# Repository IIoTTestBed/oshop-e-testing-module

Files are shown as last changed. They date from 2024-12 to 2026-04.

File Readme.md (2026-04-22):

# OSHOP Electronics Testing Module (OSH Demonstrator)

This Electronics Testing Module (OSHOP-E-Testing-Module) is an Extension of the IIoT Test Bed of the HTW Dresden. It is intended to be designed as an Open Source Hardware component within the scope of the "Open Source Hardware Innovation Platform" (OSHOP) project. In addition to its function in the IIoT Test Bed, it serves the analysis and evaluation of best practices in development under Open Source Hardware principles. The repository thus serves more for documenting the strengths and weaknesses of the Open Source concept for the development of machinery and equipment at the current time.

[TOC]

## Description

The OSHOP-E-Testing-Module extends the IIoT Test Bed of the Smart-Production-Systems group at the HTW Dresden with an Electronics Test Module. The IIoT Test Bed represents a simplified Industry 4.0 production line and demonstrates the flexible connection of several modules that can adapt to a specific product. The task of the OSHOP-E-Testing-Module is the electronic testing of a device (simplified model). The development of the OSHOP-E-Testing-Module takes place within the framework of the OSHOP project using "Open Source principles". The IIoT Test Bed is based on CP Factory Modules from the company Festo. Similarly, the OSHOP-E-Testing-Module will initially only be usable within this environment. The general value of this demonstrator lies therefore in the gained insights to simplify the development of OSH and to further advance it.

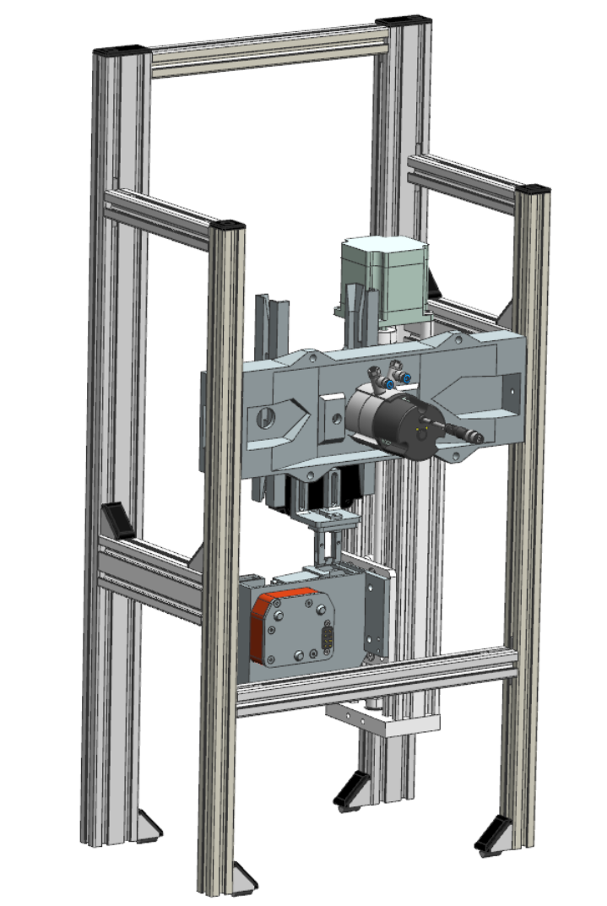
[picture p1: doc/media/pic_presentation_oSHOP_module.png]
Overview of the OSHOP-E-Testing-Module


## Procedure and Goals

- Investigation of various aspects:
    - Applicability of Git for hardware development (Open Source Hardware)
        - Version control
        - Change tracking
        - Dependency management
            - Nesting of components as Git submodules
        - Branching for collaborative work
    - Interaction/mix of proprietary and OSH designs
        - Integration of external components
- Development of an overarching intuitive/ergonomic project structure in line with frequently encountered structures in Open Source Software (OSS) repositories
    - Comparison and evaluation of various standards and OSH repositories
        - `osh-dir-std`
        - `DIN EN 81346` -> Naming conventions
    - Naming conventions
        - Testing practical naming regulations
- Bill of Materials (BOM)
    - Development of a BOM structure
    - Long-term testing of automatic generation of a BOM
        - Evaluation of submodules
        - Development of possibilities for manual modification
- Project documentation
    - Application of established procedures in OSS development
        - Documentation based on Markdown (`Readme.md`) and testing of subsequent toolchains
        - Possibilities of automation testing ("Docs Pipeline")
    - Documentation of use cases as a basis for further development in the OSHOP project
        - General development process
            - Component modeling
            - Research and integration of external free and proprietary designs
        - Git workflow
    - Identification of necessary documents regarding legal aspects
        - Function description
            - `TRL` evaluation (Basis for legal questions)
        - Assembly instructions
        - Technical documentation
            - Schematics (Pneumatics, Electricity)
            - Software
        - Software documentation
        - Hazard assessment
            - FMEA
        - Tests/Simulations
- Licensing
    - Checking compatibility of used licenses
        - Copyleft
    - License management via `REUSE` according to `SPDX`

## Status

At the moment, the demonstrator has not yet reached a functional state. Currently, the programs for controlling the drives and pneumatics are being written. Therefore, an assembly instruction and BOM can currently not be provided, as the current development processes affect the existing constructions and require constant adjustments. Furthermore, many used parts, such as hoses, cables, screws, etc., are not fully modeled. Changes therefore require constant manual updating of the documents.

This public repository includes only freely licensed designs. Proprietary models have been removed.

## Current TODOs

- TODO:
    - [ ] Manage licenses using REUSE
    - [ ] Remodeling of proprietary models to complete the public repository
    - [ ] Assembly instructions
    - [ ] Technical documentation
        - [ ] Schematics
        - [ ] Software
    - [ ] Control software
    - [ ] Documenting Git workflow
        - [ ] Branching model
    - [ ] BOM
    - [ ] Complete implementation of the documented conventions
        - [ ] Uniform naming of all files
        - [ ] Outsourcing of subassembly groups and parts into separate repositories (Submodules)

- DONE:
    - [x] Basic structuring of the project
    - [x] Initialization of Git repository and migration of models

## Dependencies

- Arduino
    - Control of the linear drive (Z-axis)
- Siemens NX
    - Needed for modifying CAD designs
- CP Factory
    - For controlling and powering the module (Electric, Pneumatic)
    - Connection to SPS
    - Festo Tec2Screen/iEasyLab for pneumatic control/tool change mechanism
- Proprietary Models
    - This public repository does not include proprietary CAD models
    - See `doc/functional_hardware_structure.md` to see which components were excluded
- Measure-Tools for the tool changer:
    - Tester:
        - `TinyProbe`: <https://github.com/wagiminator/ATtiny13-TinyProbe>
        - `Continuity Tester`: <https://github.com/wagiminator/ATtiny13-ContinuityTester>

## Project Structure

The project structure is based on the considerations of the `osh-dir-std`, but deviates from it to make it more understandable from the perspective of a constructor. This structure will undergo further changes during development.

- `doc`
    - Documentation
    - `drafts`
        - Notes and considerations, unstructured, documentation of the development process
    - `media`
        - Rendered views
        - Animations
- `src`
    - `electronic` (anticipated)
    - `hardware`
        - Contains all source CAD-files in Siemens NX `.prt` format
        - See `doc/functional_hardware_structure.md` for detailed information about the assembly and submodules
        - `printing`: STL files for printing, prototyping, analogous to the `build` or `bin` directory in software development
            - May be dropped in the future if we are able to automate the generation
    - `software`
- `LICENSES`
    - REUSE/SPDX license files for managing different licenses
- `LICENSE.md`
    - Overview of used licenses in the project
- README.md
    - Project description, general information

## License

For all self-created components, source texts, and documentation resources, the following licenses apply:

- Software: `AGPL`
- Hardware/Electronics: `CERN-OHL-S`
- Documentation: `CC-BY-SA-4.0`

Please refer the [documentation](doc/functional_hardware_structure.md) for detailed information about licensing of the used models.

## Versioning

As a convention for meaningful version numbers, we use the [Semantic Versioning Specification v2.0.0](https://semver.org/).

The version number has the following structure `MAJOR.MINOR.PATCH`.
An increase in each of the places means:

- `MAJOR` version when you make incompatible interface changes
- `MINOR` version when you add new features with backward compatibility
- `PATCH` version when you make backward compatible bug fixes or other minor changes

## Branching

For development with Git, the following branching structure was initially chosen:

| branch | meaning |
| --- | --- |
| `main` | releases of tested and documented versions |
| `documentation` | documentation of successfully tested changes merged from `testing`  |
| `testing` | testing of merged changes from `development` |
| `development` | general development |
| `dev/<feature-name>` | separated development of new feature <feature-name> |

Since proprietary models are not allowed in the public repository, this branching structure currently only exists in the internal repository.
Therefore, an OS variant is published at certain intervals.
The following diagram is intended to illustrate the workflow.

```mermaid
%%{init: {
    'logLevel': 'debug',
    'theme': 'base',
    'gitGraph': {
        'mainBranchOrder': 1
    }
}}%%
gitGraph LR:
    commit
    branch documentation order: 10
    branch testing order: 20
    branch development order: 30
    commit
    commit
    commit
    checkout testing
    merge development
    commit
    commit
    checkout documentation
    merge testing
    commit
    checkout main
    merge documentation tag: "1.0.0"
    branch "doc_osh:github/main" order: 0
    commit
    checkout main
    branch bugfix order: 21
    commit
    checkout testing
    merge bugfix
    commit
    checkout documentation
    merge testing
    checkout main
    merge documentation tag: "1.0.1"
    checkout "doc_osh:github/main"
    merge main
    checkout main
    branch "development'" order: 40
    commit
    branch "dev/feature-0815" order: 41
    commit
    checkout "development'"
    commit
    merge "dev/feature-0815"
    commit
    checkout testing
    merge "development'"
    commit
    checkout documentation
    merge "testing"
    commit
    checkout main
    merge documentation tag: "1.1.0"
    checkout "doc_osh:github/main"
    merge main id: "Clean OSH Repository"
```

**Notes**

- The branches `development` and `development'` are identical and should be displayed in the same line
- `development'` represents a `rebase` on the corresponding commit where development should continue to avoid unnecessary merges
- the plugin used for the diagram `mermaid.js` with `gitGraph` currently does not support `rebase`

## Funding

This OSH demonstrator was created as part of the Open Source Hardware Innovation Platform (OSHOP) project at HTW Dresden and is funded by the Federal Ministry for Research, Technology and Space as part of the T!Raum initiative.

BMFTR Logo
T!Raum Logo
OSHOP Logo

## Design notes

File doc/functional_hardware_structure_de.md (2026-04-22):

# Functional Structure of the Hardware
- Aufschlüsselung der funktionalen Struktur angelehnt an die DIN EN 81346

- **`e_testing_module.prt`**
    - Hauptbaugruppe
    - Rahmen aus Aluminiumprofilen
        - aus HTW-Bestand
        - TODO: kompatible Produkte recherchieren
        - Konstruktion für Festo CP Factory Modul
- **`base_module`**
    - CPFactory Grundmodul
    - Modell nicht im öffentlichen OSH-Repository enthalten
    - Hersteller/Typ: `Festo `
    - Lizenz: proprietär
    - `band_zubehör.prt`
    - `band.prt`
    - `befestigungs_rails.prt`
    - `festo_base_module_x.prt`
    - `festo_base_module.prt`
- **`linear-motion-guide_lmg`**
    - **`c-beam-linear-actuator-250mm`**
        - Linearführung (Z-Achse)
        - Basis Komponente (Design):
            - Ordner: `original`
            - Format: STEP
            - Quelle: https://grabcad.com/library/c-beam-linear-actuator-250mm-1
            - Hersteller: https://openbuildspartstore.com/c-beam-linear-actuator-bundle/
            - Lizenzvermerk: "This design incorporates OpenBuilds, LLC design work(s) shared Open Source under the CC BY-SA 4.0 License."
            - Datum: 13.06.2023
        - Probleme:
            - verwendet anderes Profil (US/Zoll), Nutensteine nicht kompatibel
            - Lizenzvermerk nur auf Webseite/Plattform vorhanden
            - Lizenz kann vom Urheber zu jedem Zeitpunkt angepasst werden
            - kein Lizenzvermerk direkt in der STEP-Datei
            - keine Lizenzdatei im Downloadarchiv vorhanden
            - dadurch keine Zuordnung zur konkreten Datei zu späterem Zeitpunkt mehr möglich
            - weitere Dokumente (Anleitungen, BOM, etc.) nur über Webseite nicht als gebündeltes Archiv versioniert
        - Steppermotor
            - Hersteller/Typ: `Nema 23`
            - wird über Arduino angesteuert
        - Aluminiumprofil
        - Montageplatten
        - Wellenkupplung
        - **`C-Beam Linear Actuator 250mm_stp.prt`**
            - Siemens NX Import von `original/C-Beam Linear Actuator 250mm.stp`
        - **`c-beam_linear_actuator_sledge.prt`**
            - Schlitten
        - **`c-beam-linear-actuator-spindle.prt`**
            - Spindel
        - **`linear_guide.prt`**
            - Baugruppe
    - **`limit-switch`**
        - Endlagensensoren
        - **`sensor_frame.prt`**
            - Halter
            - selbst konstruiert
            - Author: Valentin Petzold
            - Lizenz: CERN-OHL-S
        - `cad6084_stp.prt`
            - Siemens NX Import von `original/cad6084.stp`
            - Modell nicht im öffentlichen OSH-Repository enthalten
            - Sensoren
            - Basis Komponente (Design):
                - Hersteller/Typ: `Pepperl+Fuchs NBB2-8GM30-E2`
                - Zukaufteil
                - Datei: `original/cad6084.stp`
                - Quelle: https://www.pepperl-fuchs.com/germany/de/classid_143.htm?view=productdetails&prodid=90059
                - Lizenz: CADENAS, proprietär
    - **`mounting_adapter`**
        - **`mounting_adapter.prt`**
- **`module_structure`**
    - **`module_structure.prt`**
- **`tool_changer_system`**
    - **`Actuation_Mechanism`**
        - Hubzylinder um Werkzeugwechsel auszulösen 
        - selbst konstruiert
        - Author: Valentin Petzold
        - Lizenz: CERN-OHL-S
        - `festo_piston_rotating_mount_25mm_hub`
            - Zukaufteil
            - Modell nicht im öffentlichen OSH-Repository enthalten
            - Hersteller/Typ: `Festo ADN-16-20-A-P-A`
            - Basis Komponente (Design):
                - Ordner: `UG3DNX1926`
                - Lizenz:
                    - proprietär
                    - `readme-and-terms-of-use-3d-cad-models.txt`
                        - https://www.cadenas.de/nutzungsbedingungen-3d-cad-modelle
                            - §6 Nutzungsrechte:
                                - "[..] Er darf die abgerufenen Daten ausschließlich zum eigenen Gebrauch nutzen. Das Anfertigen von Kopien oder die Weitergabe an Dritte ist unzulässig."
        - `separator_adapter.prt`
        - `slotted pan head _ se_bolt_female.prt`
        - `slotted pan head _ se_bolt_male.prt`
    - **`Housing`**
        - Gehäuse und Halterung des Werkzeugwechselsystems
        - selbst konstruiert
        - Author: Valentin Petzold
        - Lizenz: CERN-OHL-S
        - `inner_housing_separator.prt`
            - Verbindungselement/Brücke zwischen Basishalter und Werkzeughalter
        - `Mag_Tool_Changer_Baseplate.prt`
            - Basishalter und Verbindung zur Linearführung, hält Werkzeughalter und Verriegelungsmechanismus
        - `shaft_toolhead.prt`
            - Welle, auf der Magnetverriegelung angebracht ist
    - **`Tool_Changer_Head`**
        - `Bearing 619-5.prt`
            - Kugellager, Verbindung des Drehmechanismus der Magneten mit Welle
            - Standardteil, Modell von Grabcad
            - Link: https://grabcad.com/library/bearing-619-5-1
            - Format: STEP
            - Lizenz: keine Angabe, ungeklärt, Nutzungsbedingungen von Grabcad
        - `conical_magnet.prt`
            - konischer Magnet zur Zentrierung des Werkzeugs auf dem Halter
            - Zukaufteil
            - nachkonstruiert nach Produktdatenblatt
            - Author: Valentin Petzold
            - Lizenz: CERN-OHL_S
        - `MagToolChanger_HeadBase.prt`
            - Trägerstruktur/Gehäuse, Verknüpfung zum `Housing` und Wechselmechanismus
            - angepasste Konstruktion siehe `Tool_changer_osh_original_files`
        - `MagToolChanger_Lockplate.prt`
            - drehbare Platte mit Magneten, wird durch Pneumatik-Kolben angetrieben
            - vorher `MagToolChanger_Lockplate_part1.prt`
        - `MagToolChanger_Lockplate_part2.prt`
            - obsolet, da per Druckparameter Hohlraum überbrückt werden kann, Druck also mit einem Modell möglich ist
        - `plate_magtoolchanger_headbase.prt`
            - Abdeckung und Halterung für konische Magneten
        - `tool_changer_rotation_plate.prt`
            - obsolet, erster Entwurf des `tool_storage_system`
    - `Tool_changer_osh_original_files`
        - Werkzeugwechselsystem, OSH
        - Quelle: https://github.com/totaldesaster/toolchanger
        - Lizenz: GPLv3
    - **`Toolhead Assembly_stp.prt`**
- **`tool_storage_system`**
    - Werkzeuglager
    - **`drvs12-rot_motor`**
        - Antrieb zum Schwenken des Werkzeughalters
        - Modell nicht im öffentlichen OSH-Repository enthalten
        - Zukaufteil
        - Hersteller/Typ: `Festo DRVS-12-180-P`
        - Ordner: `UG3DNX1926`
        - Lizenz: Nutzungsbedingungen von CADENAS, <https://www.cadenas.de/nutzungsbedingungen-3d-cad-modelle>, proprietär
        - erweitert mit Endlagensensor: `Festo SRBS-Q12-12`
            - Modelle siehe oben
    - **`mounting`**
        - Aufnahme des Werkzeughalters
        - selbst konstruiert
        - Author: Valentin Petzold
        - Lizenz: CERN-OHL-S
        - **`mounting_storage.prt`**
            - Befestigung des Werkzeuglagers am Rahmen
            - wg. Druckbarkeit in 2 Teile aufgeteilt (`*_{p1|p2}.prt`)
        - **`spacer_storagemount_rotdev.prt`**
            - Abstandshalter zwischen Antrieb und Halterung
            - Justierung des Abstands zwischen Werkzeuglager und Halterung
    - **`tool_holder`**
        - Werkzeughalter
        - selbst konstruiert
        - Author: Valentin Petzold
        - Lizenz: CERN-OHL-S
        - **`tool_storage_part1.prt`**
            - symmetrisch, muss doppelt gedruckt und montiert werden
        - **`spacer_storage_mounting`**
            - Adapter für Flansch zu Werkzeughalter
    - **`tool_locking_system`**
        - Werkzeug Verriegelung
        - **`clamp`**
            - Klemme zur Arretierung des Werkzeugs 
            - `tool_storage_lock_plate`
                - selbst konstruiert
                - Author: Valentin Petzold
                - Lizenz: CERN-OHL-S
                - TODO: Muttern modellieren --> Montageanleitung
        - `dummies`
            - `dummy_piston.prt`
                - Dummy zum testen der mechanischen Verriegeln des Werkzeughalters
                - später durch pneumatischer Kolben ersetzt
            - `pull_clip.prt`
                - Clip zum mechanischen Verriegeln
        - **`piston_actuator/advc-10-10-apa-kurzhub`**
            - Kolben um Klemmung auszulösen
            - Zukaufteil
            - Modell nicht im öffentlichen OSH-Repository enthalten
            - Hersteller/Typ: `Festo ADVC-10-10-APA`
            - Lizenz: CADENAS, proprietär
            - Probleme:
                - verwendete Modelle von Festo waren kleiner als die realen Abmaße des gelieferten Kolbens
        - **`piston_mounting_structure`**
            - Halterung für den Kolben
            - Komponenten:
                - `piston_mounting_frame`
                - `piston_mounting_plate`
            - Probleme:
                - Halter liegt sehr eng an Kolben an, erfordert u.U. immer Anpassung an Modelle anderer Hersteller
                - Befestigungsschrauben nicht mit modelliert
                - könnte eleganter konstruiert werden durch montage am vorderen Ende, eher Konstruktionsschwäche des Kolbens
            - selbst konstruiert
            - Author: Valentin Petzold
            - Lizenz: CERN-OHL-S
        - **`tool_storage_print_vers.prt`**
- **`tools`**
    - `plate_tool_board.prt`
    - `spacer_10x3.6_id3.prt`

- noch nicht im Modell enthalten:
- Treibermodul
    - wandelt Befehle vom Mikrocontroller in elektrische Signale an den Motor um (Rechtecksignal)
    - Hersteller/Typ: `ACT Motor DM 542`
- Microcontroller
    - Hersteller/Typ: `Arduino M0 Pro`
- Pneumatik
    - Ventilinsel
        - Hersteller/Typ: `Festo`
        - TODO: genaue Bezeichnung ergänzen!
- Dockingmodul:
    - Schnittstelle zu Tablet/CP-Factory-Modul
    - Hersteller/Typ: `Festo +G1:XD12`

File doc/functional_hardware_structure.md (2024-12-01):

# Functional Structure of the Hardware
- Breakdown of the functional structure based on DIN EN 81346

- **`e_testing_module.prt`**
    - Main assembly
    - Frame made of aluminum profiles
        - from HTW stock
        - TODO: search for compatible products
        - Construction for Festo CP Factory Module
- **`base_module`**
    - CPFactory base module
    - Model not included in the public OSH-Repository
    - Manufacturer/Type: `Festo`
    - License: proprietary
    - `band_zubehör.prt`
    - `band.prt`
    - `befestigungs_rails.prt`
    - `festo_base_module_x.prt`
    - `festo_base_module.prt`
- **`linear-motion-bearing`**
    - **`c-beam-linear-actuator-250mm`**
        - Linear actuator (Z-axis)
        - Basic component (Design):
            - Folder: `original`
            - Format: STEP
            - Source: https://grabcad.com/library/c-beam-linear-actuator-250mm-1
            - Manufacturer: https://openbuildspartstore.com/c-beam-linear-actuator-bundle/
            - License notice: "This design incorporates OpenBuilds, LLC design work(s) shared Open Source under the CC BY-SA 4.0 License."
            - Date: 13.06.2023
        - Issues:
            - Uses a different profile (US/inch), dowels used in the main assembly are not compatible
            - License notice only available on the website/platform
            - License can be adjusted by the author at any time
            - No license notice directly in the STEP file
            - No license file in the download archive available
            - Therefore, no assignment to the specific file possible at a later time
            - Further documents (instructions, BOM, etc.) only available over the website not versioned as a bundled archive
        - Stepper motor
            - Manufacturer/Type: `Nema 23`
            - Controlled via Arduino
        - Aluminum profile
        - Mounting plates
        - Wave coupling
        - **`C-Beam Linear Actuator 250mm_stp.prt`**
            - Siemens NX import of `original/C-Beam Linear Actuator 250mm.stp`
        - **`c-beam_linear_actuator_sledge.prt`**
            - Sledge
        - **`c-beam-linear-actuator-spindle.prt`**
            - Spindle
        - **`linear_guide.prt`**
            - Assembly
    - **`limit-switch`**
        - End switch sensors
        - **`sensor_frame.prt`**
            - Holder
            - Self-constructed
            - Author: Valentin Petzold
            - License: CERN-OHL-S
        - `cad6084_stp.prt`
            - Siemens NX import of `original/cad6084.stp`
            - Model not included in the public OSH-Repository
            - Sensors
            - Basic component (Design):
                - Manufacturer/Type: `Pepperl+Fuchs NBB2-8GM30-E2`
                - Purchase part
                - File: `original/cad6084.stp`
                - Source: https://www.pepperl-fuchs.com/germany/de/classid_143.htm?view=productdetails&prodid=90059
                - License: CADENAS, proprietary
    - **`mounting_adapter`**
        - **`mounting_adapter.prt`**
- **`module_structure`**
    - **`module_structure.prt`**
- **`tool_changer_system`**
    - **`Actuation_Mechanism`**
        - Piston cylinder to trigger tool change
        - Self-constructed
        - Author: Valentin Petzold
        - License: CERN-OHL-S
        - `festo_piston_rotating_mount_25mm_hub`
            - Purchase part
            - Model not included in the public OSH-Repository
            - Manufacturer/Type: `Festo ADN-16-20-A-P-A`
            - Basic component (Design):
                - Folder: `UG3DNX1926`
                - License:
                    - proprietary
                    - `readme-and-terms-of-use-3d-cad-models.txt`
                        - https://www.cadenas.de/nutzungsbedingungen-3d-cad-modelle
                            - §5 Terms of Use:
                                - "[..] The customer may use the retrieved data for personal uses only."
        - `separator_adapter.prt`
        - `slotted pan head _ se_bolt_female.prt`
        - `slotted pan head _ se_bolt_male.prt`
    - **`Housing`**
        - Housing and mounting of the tool change system
        - Self-constructed
        - Author: Valentin Petzold
        - License: CERN-OHL-S
        - `inner_housing_separator.prt`
            - Connection element/bridge between the base holder and tool holder
        - `Mag_Tool_Changer_Baseplate.prt`
            - Base holder and connection to the linear actuator, holds the tool holder and locking mechanism
        - `shaft_toolhead.prt`
            - Shaft, on which the magnetic lock is mounted
    - **`Tool_Changer_Head`**
        - `Bearing 619-5.prt`
            - Bearing, connection of the rotating mechanism of the magnets with the shaft
            - Standard part, model from Grabcad
            - Link: https://grabcad.com/library/bearing-619-5-1
            - Format: STEP
            - License: none provided, unclear, usage terms of Grabcad
        - `conical_magnet.prt`
            - Conical magnet for centering the tool on the holder
            - Purchase part
            - Redesigned according to product data sheet
            - Author: Valentin Petzold
            - License: CERN-OHL_S
        - `MagToolChanger_HeadBase.prt`
            - Carrier structure/housing, connection to the `Housing` and locking mechanism
            - Adapted construction see `Tool_changer_osh_original_files`
        - `MagToolChanger_Lockplate.prt`
            - Rotating plate with magnets, driven by a pneumatic cylinder
            - Previously `MagToolChanger_Lockplate_part1.prt`
        - `MagToolChanger_Lockplate_part2.prt`
            - Obsolete, as the gap can be bridged with a print parameter, making a print possible with a model
        - `plate_magtoolchanger_headbase.prt`
            - Cover and holder for conical magnets
        - `tool_changer_rotation_plate.prt`
            - Obsolete, first draft of the `tool_storage_system`
    - `Tool_changer_osh_original_files`
        - Tool change system, OSH
        - Source: https://github.com/totaldesaster/toolchanger
        - License: GPLv3
    - **`Toolhead Assembly_stp.prt`**
- **`tool_storage_system`**
    - Tool storage
    - **`drvs12-rot_motor`**
        - Drive for swinging the tool holder
        - Model not included in the public OSH repository
        - Purchase part
        - Manufacturer/Type: `Festo DRVS-12-180-P`
        - Folder: `UG3DNX1926`
        - License: Terms of use by CADENAS, <https://www.cadenas.de/nutzungsbedingungen-3d-cad-modelle>, proprietary
        - Extended with end stop sensor: `Festo SRBS-Q12-12`
            - Models see above
    - **`mounting`**
        - Mounting of the tool holder
        - Self-constructed
        - Author: Valentin Petzold
        - License: CERN-OHL-S
        - **`mounting_storage.prt`**
            - Mounting of the tool storage to the frame
            - Due to printability, divided into 2 parts (`*_{p1|p2}.prt`)
        - **`spacer_storagemount_rotdev.prt`**
            - Spacer between drive and mounting
            - Adjustment of the distance between tool storage and mounting
    - **`tool_holder`**
        - Tool holder
        - Self-constructed
        - Author: Valentin Petzold
        - License: CERN-OHL-S
        - **`tool_storage_part1.prt`**
            - Symmetrical, must be printed and mounted twice
        - **`spacer_storage_mounting`**
            - Adapter for flange to tool holder
    - **`tool_locking_system`**
        - Tool locking
        - **`clamp`**
            - Clamp for securing the tool
            - `tool_storage_lock_plate`
                - Self-constructed
                - Author: Valentin Petzold
                - License: CERN-OHL-S
                - TODO: Model screws --> Assembly instructions
        - `dummies`
            - `dummy_piston.prt`
                - Dummy for testing the mechanical locking of the tool holder
                - Later replaced by a pneumatic piston
            - `pull_clip.prt`
                - Clip for mechanical locking
        - **`piston_actuator/advc-10-10-apa-kurzhub`**
            - Piston to trigger clamping
            - Purchased part
            - Model not included in the public OSH repository
            - Manufacturer/Type: `Festo ADVC-10-10-APA`
            - License: CADENAS, proprietary
            - Issues:
                - The Festo models used were smaller than the actual dimensions of the delivered piston
        - **`piston_mounting_structure`**
            - Mounting for the piston
            - Components:
                - `piston_mounting_frame`
                - `piston_mounting_plate`
            - Issues:
                - The mounting is very tight on the piston, requires adjustment for models from other manufacturers
                - Mounting screws not modeled
                - Could be more elegantly constructed by mounting at the front end, rather a construction weakness of the piston
            - Self-constructed
            - Author: Valentin Petzold
            - License: CERN-OHL-S
        - **`tool_storage_print_vers.prt`**
- **`tools`**
    - `plate_tool_board.prt`
    - `spacer_10x3.6_id3.prt`

- not yet included in the model:
- Driver module
    - Converts commands from the microcontroller into electrical signals for the motor (rectangular signal)
    - Manufacturer/Type: `ACT Motor DM 542`
- Microcontroller
    - Manufacturer/Type: `Arduino M0 Pro`
- Pneumatics
    - Valve assembly
        - Manufacturer/Type: `Festo`
        - TODO: Add exact designation!
- Docking module:
    - Interface to tablet/CP-Factory module
    - Manufacturer/Type: `Festo +G1:XD12`

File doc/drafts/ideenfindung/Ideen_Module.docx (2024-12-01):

Ventilinsel:

https://www.thingiverse.com/thing:3186352

https://www.thingiverse.com/thing:3142024

https://www.thingiverse.com/thing:3141922

https://www.thingiverse.com/thing:1581203

https://www.thingiverse.com/thing:3985559

https://www.thingiverse.com/thing:2798873

https://www.thingiverse.com/thing:2326265

https://www.thingiverse.com/thing:3808689

https://www.thingiverse.com/thing:2926583

https://www.thingiverse.com/thing:2873796

https://www.thingiverse.com/thing:4754779

https://www.thingiverse.com/thing:2738707

https://www.thingiverse.com/thing:3066355

Einkaufliste:

Pneumatikzylinder:

https://www.pneumaticshop.de/Pneumatikzylinder/

https://www.smc.eu/de-de/produkte/cqs~16708~nav?productId=164339&partNumber=CDQSB12-25D

https://www.reichelt.de/kompaktzylinder-c9585.html?&nbc=1

https://www.festo.com/de/de/p/kompaktzylinder-doppeltwirkend-id_ADN_S/?page=0

https://pneumatikteam.de/pneumatik/zylinder/kurzhubzylinder/

https://www.ventile24.de/cdqsyb25-5dc-smc-pneumatik-c-d-qsy-druckluftzylinder-gleichmassig-leichtlauf-doppeltwirkend-eingebauter-magnetring-durchgangsbohrung-gewinde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

https://www.nettechnic.de/pneumatischer-kompaktzylinder-doppeltwirkend-20x20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

Pneumatischer Schwenkantrieb:

https://www.smc.eu/de-de/produkte/crb2-z~124774~nav?productId=124776&partNumber=CDRB2FWU20-90DZ

https://de.rs-online.com/web/c/pneumatik-und-hydraulik/pneumatik-zylinder-und-antriebe/pneumatische-drehantriebe/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

https://www.landefeld.de/artikel/de/drvs-6-180-p-1845707-schwenkantrieb/OT-FESTO057650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

Drehverteiler Druckluft:

https://www.festo.com/de/de/p/drehverteiler-id_GF/?page=0&q=~%3AfestoSortOrderScored

oder:

https://www.festo.com/de/de/a/177717/?q=~:festoSortOrderScored

+

https://www.landefeld.de/artikel/de/qsr-m5-6-153527-rotations-steckverschraubung/OT-FESTO015490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

Ventilinsel:

https://www.landefeld.de/artikel/de/vqc4301r-51-smc-53-wegeventil/OT-SMC069682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

Steckverschraubungen:

https://www.festo.com/de/de/p/steckverschraubung-id_QS/?page=0

Magnete:

https://deinemagneten.de/produkt/neodym-magnete-o-10x3-mm-n52-scheiben-rundmagnet-starkmagnete-supermagnete/

https://www.magnet-shop.net/neodym-magnete/scheibenmagnete/scheibenmagnet-10.0-x-1.0-mm-n35-nickel-haelt-500-g

quaderscheibe.

https://www.magnet-shop.net/neodym-magnete/quadermagnete/quadermagnet-10.0-x-10.0-x-2.0-mm-n45-nickel-haelt-1.2-kg

Kegel und Senke-Magnet:

https://www.first4magnets.com/de/magnetmaterialien-standardbaugruppen-c150/10mm-durchmesser-x-2mm-dicke-x-3mm-c-sink-neodym-magnet-1-2kg-zugkraft-p2446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

Tools:

Testmodule:

-Shaker

-Lötstellenprüfer

-Gewichtsprüfer

Produktionsmodule:

-Handlager zu Magazin Befüller

-Sicherung entnehmen

-Handlager Sensorik

-2-Achs Roboter

-Werkzeugwechsleraufnahme (flex führung und stromversorgung)

-modifizierter Carrier

-Kistenhub

-Transportmodul zwischen zwei Lagern

https://www.google.com/url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 (https://www.google.com/url?psig=AOvVaw2psAzcrv_vjG3QuWZ-ws1R&cd=vfe)

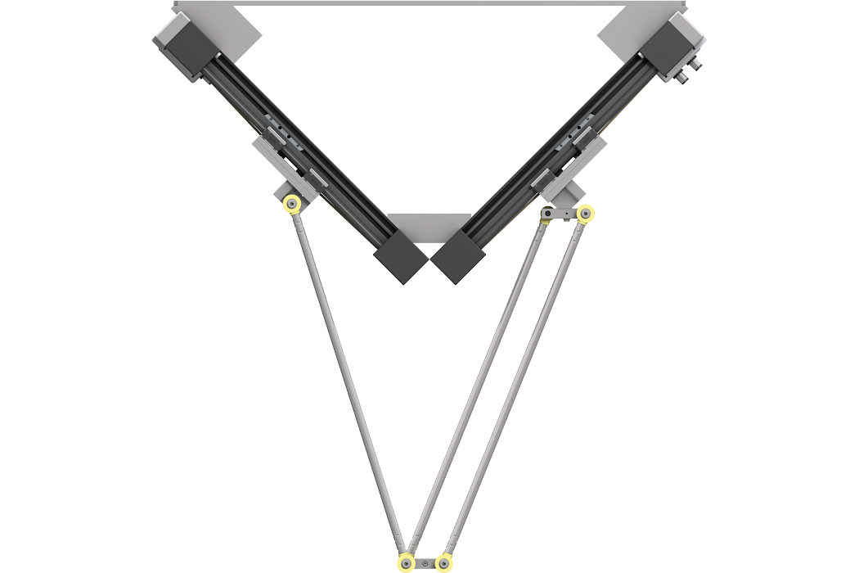
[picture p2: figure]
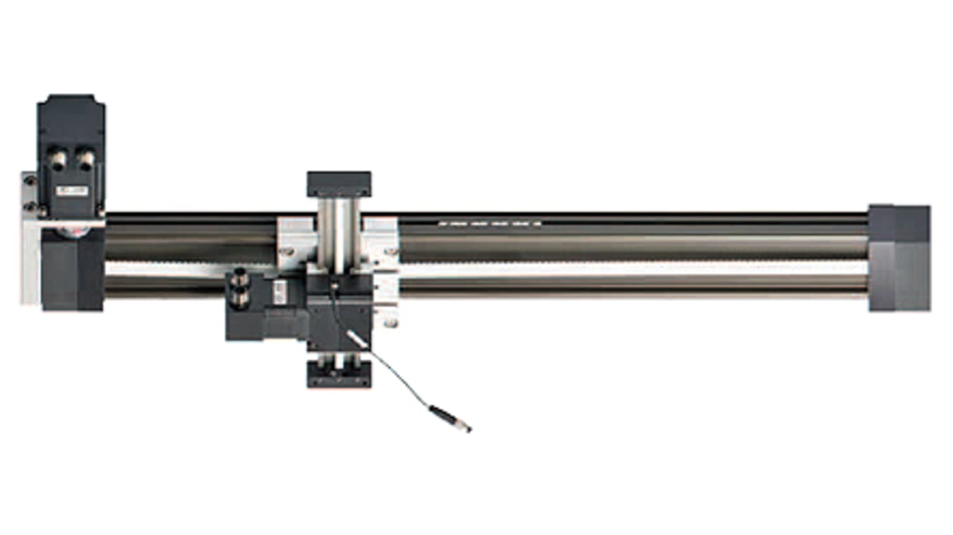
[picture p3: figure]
Igus DLE-LG-0001 2-Achsen Linearer Roboter, Arbeitsraum 500 x 100mm, bis 2.5kg | RS
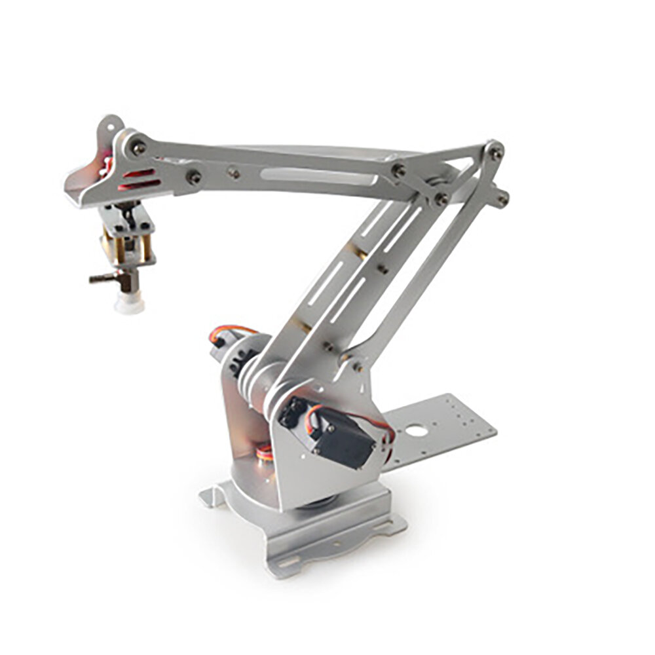
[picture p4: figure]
3 DOF Palettierroboterarm 3-Achsen-Roboter DIY 3D-Drucker mit 180 ° MG996R Servo für die Roboterausbildung Sale - Banggood Deutschland sold out-arrival notice-arrival notice

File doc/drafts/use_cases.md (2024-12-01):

# Use Case Teile-Konstruktion
1. Neues Projekt starten
    - Projektordner anlegen (Grundstruktur)

2. Zielbeschreibung
    - grobes Konzept erarbeiten
    - Erfahrung mit oSHOP Projekt:
        - grobe Vorgabe: Entwicklung eines "faszinierenden" Moduls (mit Bewegung etc.) für Festo CP Factory
        - eigenes Ziel: Projekt mit Nutzen für Arbeitsgruppe, daher: Gespräche mit Kollegen was im Moment noch in CP Factory ergänzt werden könnte bzw. bei welchen Konzepten Probleme bestehen
        - Ergebnis: Ideen zu Toolchanger, eigene Idee zur Prüfung der Leiterplatten welche in CP Factory verarbeitet werden (da diese Funktion noch nicht in Fertigungskette vorhanden) --> Kombination dieser Ideen als Ziel des Projekts
    --> Ableiten erster Anforderungen und Rahmenbedingungen (zum Beispiel Breite/Abstand/Art der Schienen zur Montage auf dem CP Factory Modul)

3. Freie Recherche vorhandener Lösungen
    - keine zentrale, herstellerübergreifende Teiledatenbank
        - gute Beispiele: 
            - speziell für Satellitenentwicklung: https://satsearch.co
        - grobe Kategorisierung
            - Material
    - Doppelentwicklung vermeiden
    - einsparen von Entwicklungsaufwand
    - Wenn es keine fertige Lösung gibt, Neuentwicklung:
        - Recherche nach ähnlichen Lösungsansätzen, Konzepten, Prinzipien
            - hauptsächlich Internet, Webseiten
            - rein visuell anhand von Bildern
                - finden von geeigneten CAD-Modellen schwierig, da aktuelle Plattformen sehr viele unprofessionelle (DIY) Lösungen enthalten
            - viele Repositories (z.B. GitHub) nur textuell beschrieben, sehr aufwendig jeden Fund manuell zu prüfen
    - Erfahrung mit oSHOP Projekt:
        - Recherche nach bestehenden Konzepten rund um Thema Tool Changer und Prüf- bzw. Messverfahren von Leiterplatten
        - ``TinyProbe`` and ``TinyTester`` als Konzepte für Messverfahren identifiziert --> wenig Adaption nötig
        - MagToolChanger als Konzept für Werkzeugwechsel identifiziert --> viel Adaption nötig, Anmerkung: bereits der gefundene Ansatz wurde vom Hersteller E3D inspiriert
            - E3D fertigt kommerziell Werkzeugwechselsystem für 3D Drucker unterstützt aber OSH und stellt teilweise Schemata online
    -- >Ergänzen der Grundanforderungen aus 2. um die Anforderungen resultierend aus selektierten Konzepten

    3.1 Nach Taxonomie Maschinenelemente/Standardteile
        - Grund: Adaption oder Ergänzung der selektierten Konzepte aus 2.
        - Beispiel: Pneumatikzylinder
            - bestimmen von Parametern:
                - erforderlicher Hubweg
                - welche Kräfte treten auf
                - Bewegungscharakteristik (linear, kreisbahn, ...)
            - anhand der Parameter Bestimmung des Kolbendurchmessers nach Herstellern (Kataloge, Webseiten)
            - Bewertung Herstellerauswahl hinsichtlich
                - Bauteilgröße
                - Schnittstellen
                    - zu bereits verwendeten Komponenten, wie Pneumatikschläuche
                    - Notwendigkeit von Adaptern
                    - Befestigung
                - Verfügbarkeit von CAD-Modellen:
                    - Festo: sehr gut
        --> Erweiterung der Anforderungen um zusätzliche Bedingungen durch ausgewählte Maschinenelement bzw. Standardteile

    3.2 Patentrecherche bzw. Verletzung Rechte Dritte
        - Wie hoch ist der tendenzielle Schaden im Falle einer Patentrechtsverletzung?
            - Unterlassung der Produktion/Verkauf
            - nachträglicher Erwerb einer Patentlizenz
            - Schadensforderung (Gewinnausfall des Patentinhabers usw.)
        --> Erbringungen ``freedom to operate`` für den Projektentwurf

AB HIER EIN ITERATIONSPROZESS

4. Adaption der gefundenen Lösungsansätze
    - auf die aufgestellten Anforderungen
    - mit den geplanten Maschinenelementen/Standardteilen

5. Entwurf eigener Interfaces anhand zur Verknüpfung der gefundenen (und adaptierten) Lösungsansätze
    - Verknüpfung aller Konzepte zu vollständiger (Unterbaugruppe)-Baugruppe
    --> zum Beispiel durch Entwurf von Gehäusen, Adaptern, Interfaces etc.

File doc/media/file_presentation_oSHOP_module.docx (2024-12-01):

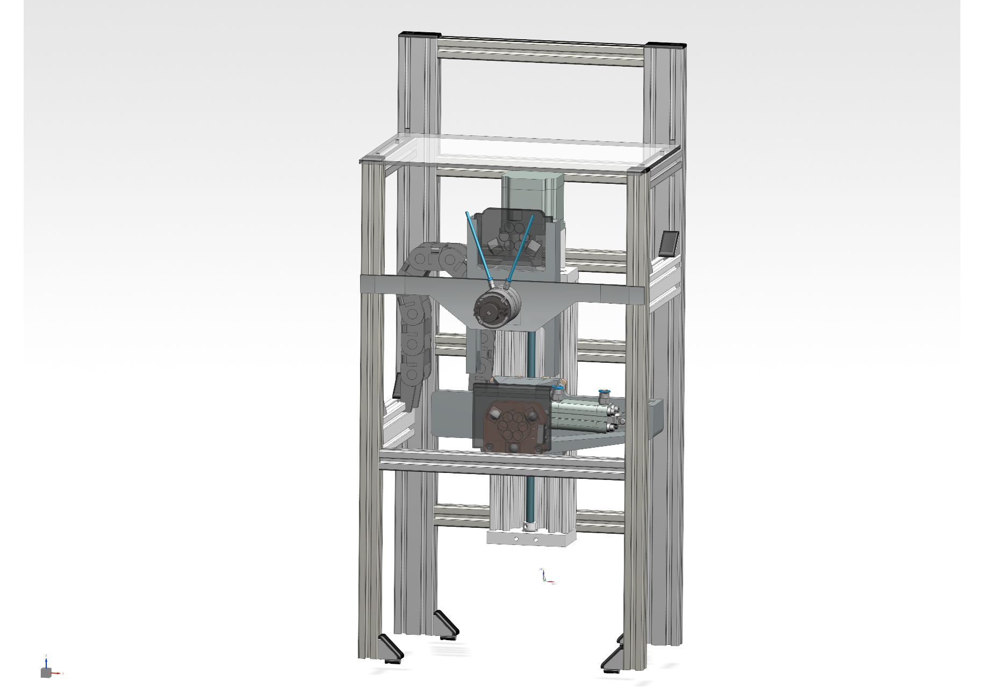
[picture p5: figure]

Open Source Hardware Werkzeuge Zum Beispiel Bestückung mit einer Platine zum Test der elektrischen Funktionalität von Werkstücken

Open Source Energiekette

Publiziert von privatem Entwickler auf Thingiverse.com

CC BY 4.0 License

Open Source Linearführung Vertrieb und Design durch OpenBuilds Store

CC BY-SA 4.0 License

Open Source Werkzeugwechselsystem

Weiterentwickelt für pneumatische Ansteuerung auf einer Linearachse

GNU General Public License V3

Werkzeuglager für Werkzeugwechselsystem

Eigenentwicklung in Vorbereitung zur Publikation als Open Source Hardware

This design incorporates OpenBuilds, LLC (https://openbuilds.com/)design work(s) shared Open Source under the CC BY-SA 4.0 (https://creativecommons.org/licenses/by-sa/4.0/) License.

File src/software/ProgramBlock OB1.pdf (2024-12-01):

## Totally Integrated Automation Portal

# Oshop-Demo_v2 / PLC_1 [CPU 1512SP-1 PN] / Programmbausteine

# Main [OB1]

## Main Eigenschaften Allgemein

Name | Main | Nummer | 1 | Typ | OB | Sprache | KOP
Nummerierung | Automatisch

## Information

Titel | "Main Program Sweep (Cy‐ cle)" | Autor | Kommentar | Familie
Version | 0.1 | Anwenderdefi‐ nierte ID

## Main

Name | Datentyp | Defaultwert | Kommentar

## Input

Initial_Call | Bool | | Initial call of this OB
Remanence | Bool | | =True, if remanent data are available

## Temp

Pos | DInt
RetVal | DInt
tmpByte | Byte

## Constant

# Netzwerk 1:

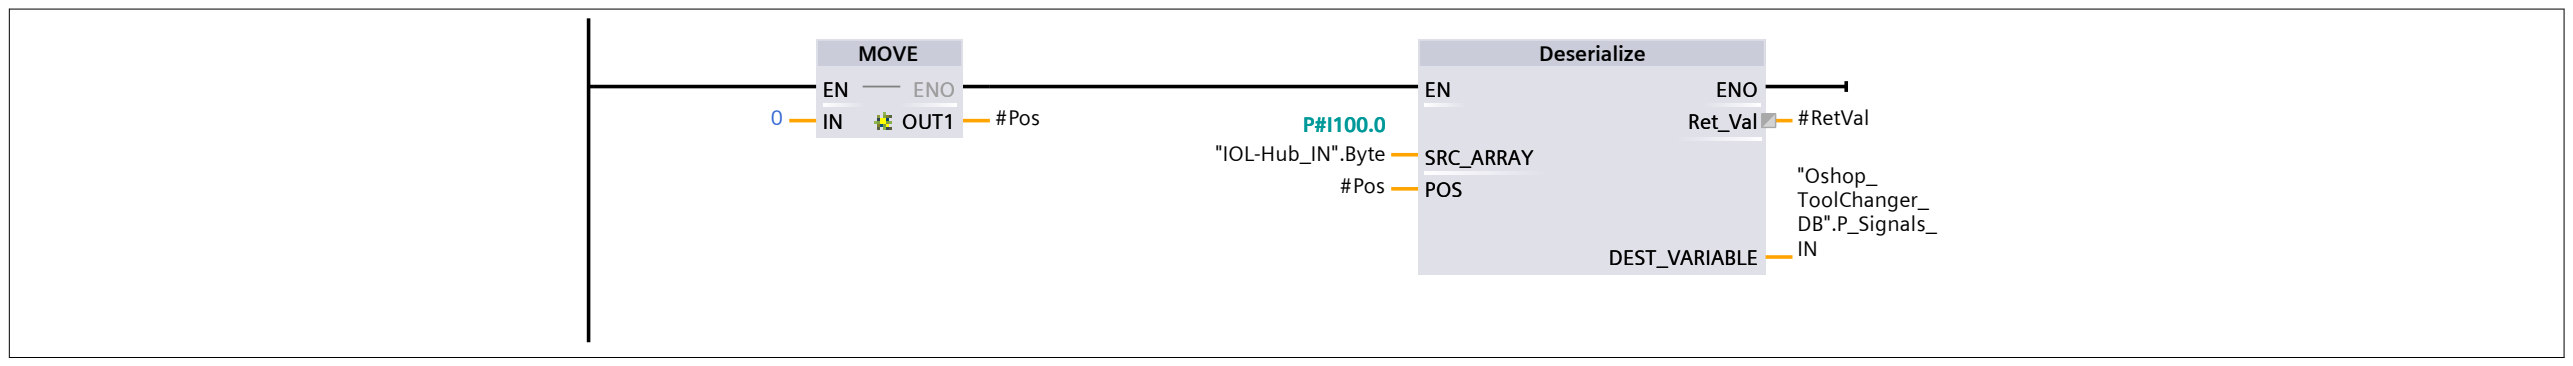
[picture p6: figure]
MOVE; Deserialize; 0 #Pos; "IOL-Hub_IN".Byte P#I100.0; #Pos; #RetVal; "Oshop_ ToolChanger_ DB".P_Signals_ IN; ENO OUT1; SRC_ARRAY POS; ENO Ret_Val; DEST_VARIABLE

# Netzwerk 2:

"Tool_Select"

%FB2

"Tool_Select_DB"

%DB3

"Taster_WH_1"

%I0.1

"Taster_WH_2"

%I0.2

"Lampe_WH_1"

%Q0.1

"Lampe_WH_2"

%Q0.2

0

EN

Button_1

Button_2

ENO

Lamp_1

Lamp_2

ToolNumber EN

Button_1

Button_2

ENO

Lamp_1

Lamp_2
ToolNumber

# Netzwerk 3:

"Oshop_ToolChanger"

%FB1

"Oshop_
ToolChanger_
DB"

%DB1

"Taster_Grün"

%I0.0

"Tool_Select_ DB".ToolNumber

... EN

Start

UseTool
P_Signals_IN

ENO

P_Signals_OUT EN

Start

UseTool
P_Signals_IN

ENO
P_Signals_OUT

# Netzwerk 4:

FILL_BLK

0
1 "IOL-Hub_OUT".
Byte[1]

%QB101

EN
IN
COUNT

ENO

OUT

# Netzwerk 5:

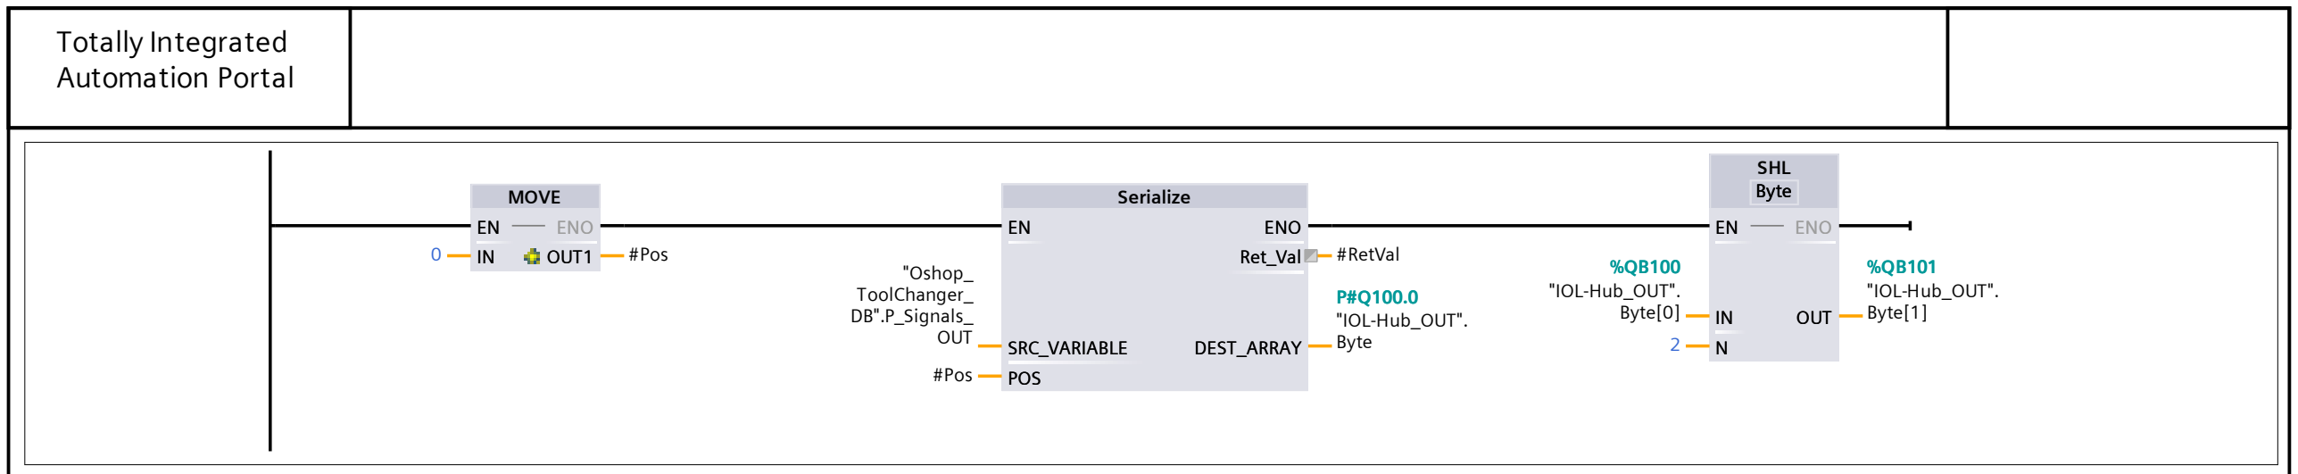
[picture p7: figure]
Totally Integrated Automation Portal; MOVE; Serialize; SHL Byte; 0 #Pos; "IOL-Hub_OUT". Byte; "IOL-Hub_OUT". Byte[0]; "IOL-Hub_OUT". Byte[1]; ENO OUT1; SRC_VARIABLE POS; ENO Ret_Val; DEST_ARRAY; ENO; OUT; Byte EN; Byte

"Oshop_ ToolChanger_ DB".P_Signals_ OUT #Pos | #RetVal

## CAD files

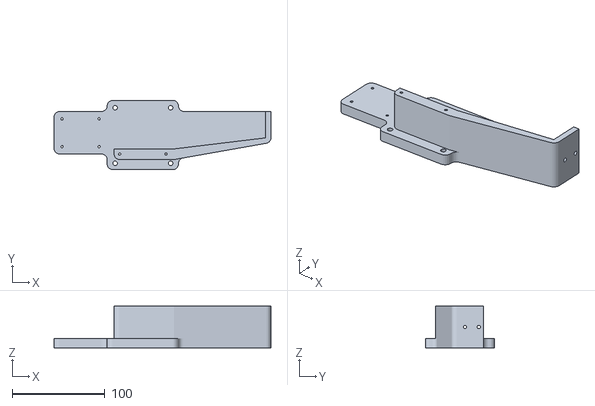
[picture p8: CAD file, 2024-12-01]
gen/manuf/fdm/Mag_Tool_Changer_Baseplate.stl
234.5 x 74.8 x 45.0

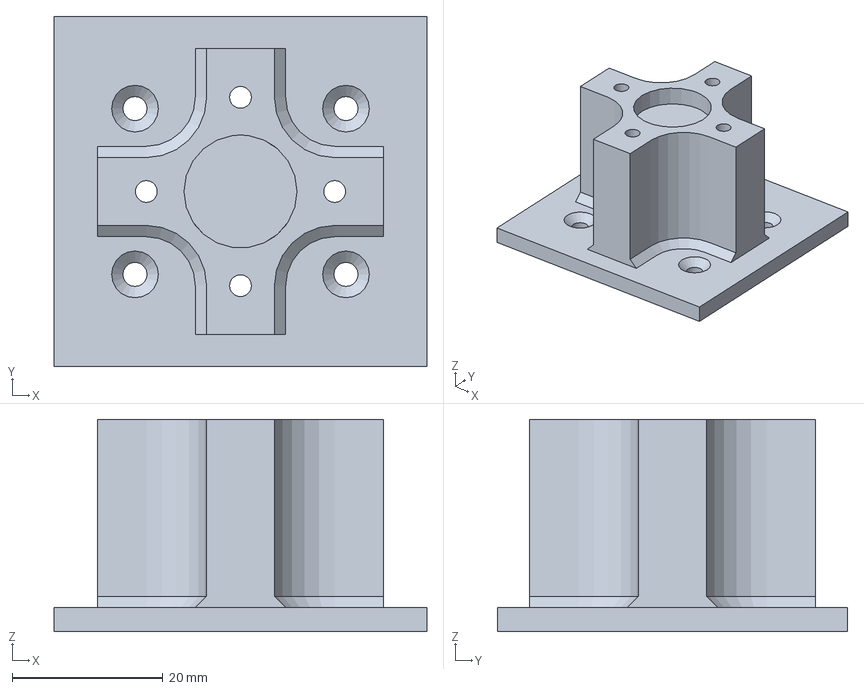
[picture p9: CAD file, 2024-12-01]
gen/manuf/fdm/new/drag_chain.3mf
49.5 x 46.5 x 28.2 mm

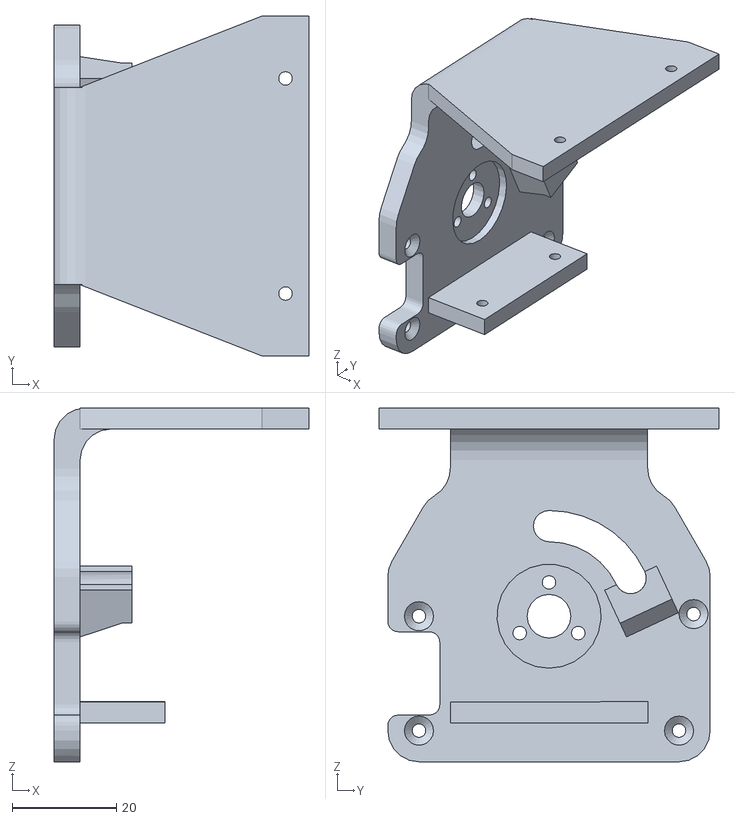
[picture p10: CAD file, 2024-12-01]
gen/manuf/fdm/new/lennart/inner_housing_separator_2.stl
49.0 x 65.4 x 68.0

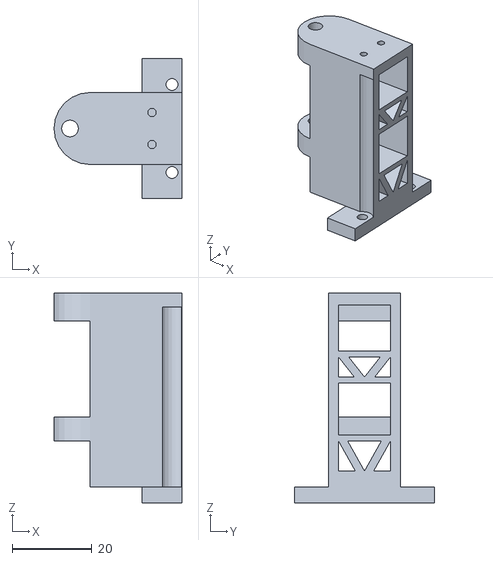
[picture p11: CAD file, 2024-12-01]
gen/manuf/fdm/new_2024/piston_mounting_frame_a_guiding_1.stl
32.0 x 35.0 x 52.5

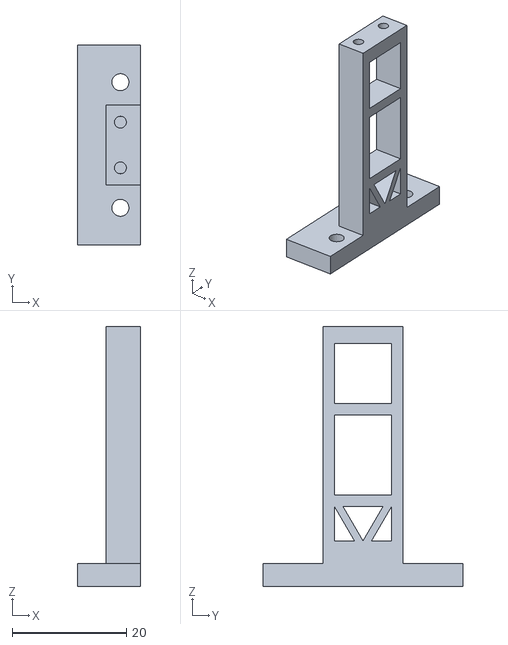
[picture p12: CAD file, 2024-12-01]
gen/manuf/fdm/new/storage_piston_mount.stl
11.0 x 35.0 x 45.5

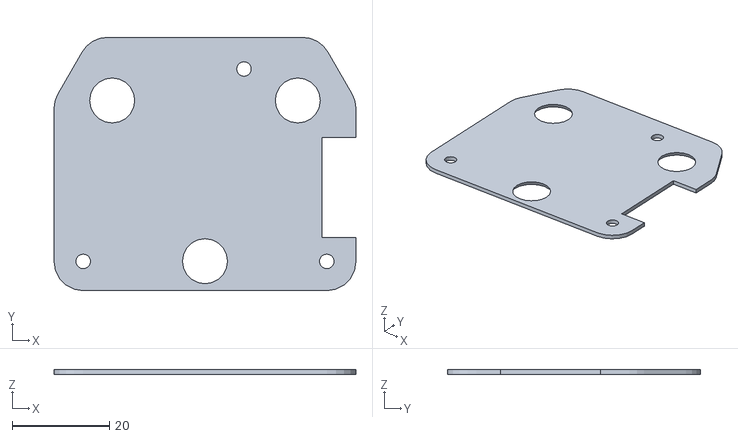
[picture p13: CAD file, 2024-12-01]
gen/manuf/fdm/plate_magtoolchanger_headbase.stl
62.0 x 52.0 x 1.00

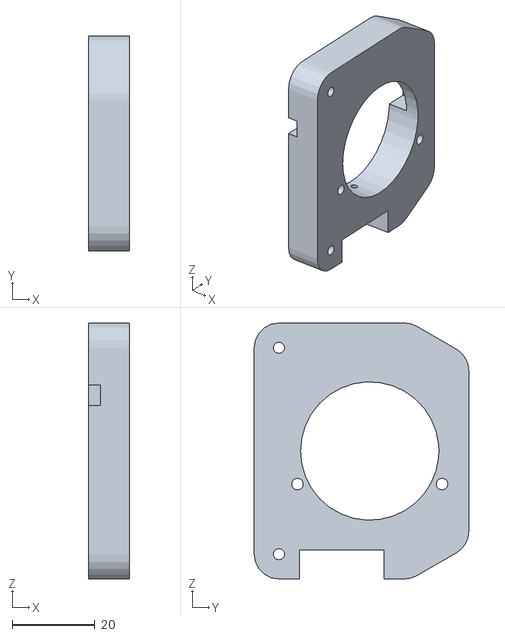
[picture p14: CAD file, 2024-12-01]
gen/manuf/fdm/MagToolChanger_HeadBase_1.stl
10.0 x 52.0 x 62.0

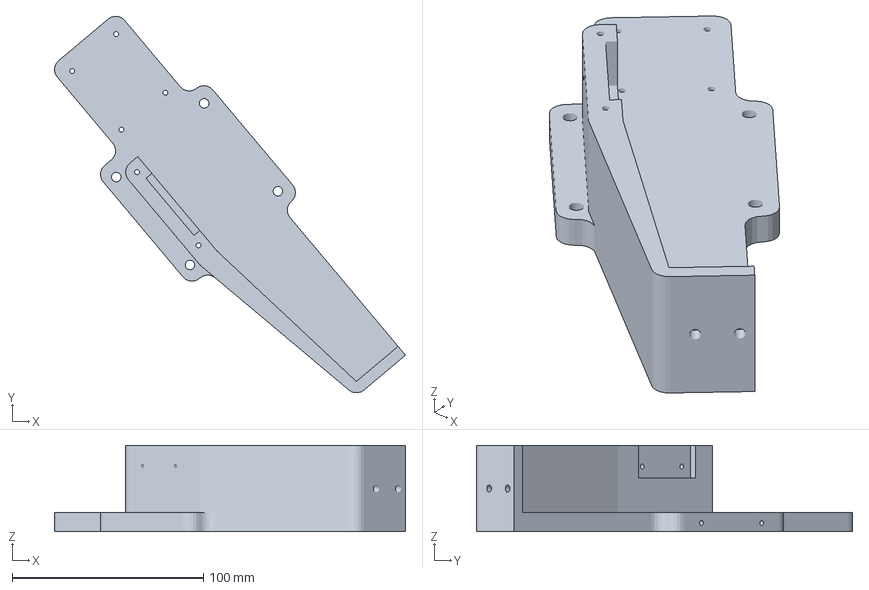
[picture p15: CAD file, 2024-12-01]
gen/manuf/fdm/new/ground_plate_tool_changer.3mf
183.5 x 196.8 x 45.0 mm

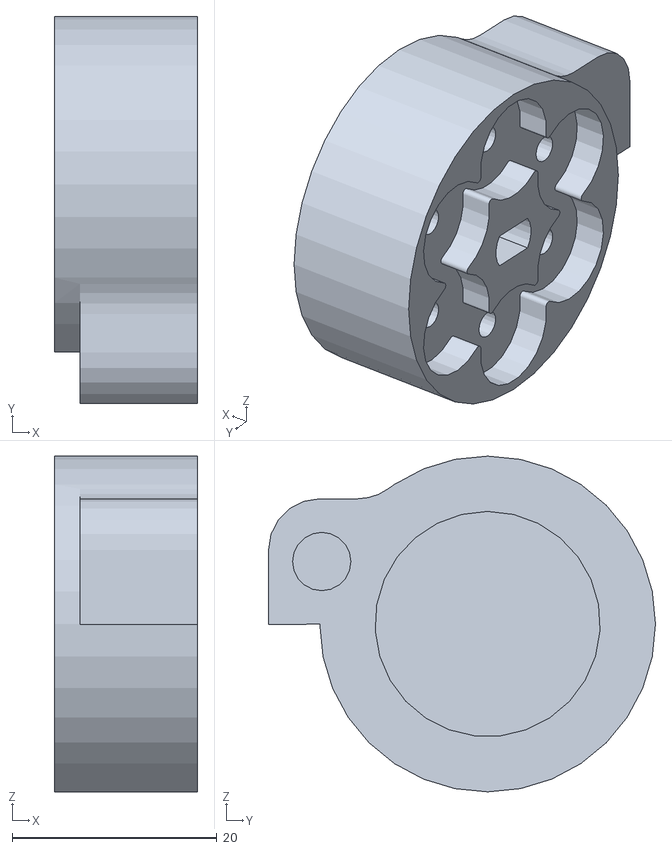
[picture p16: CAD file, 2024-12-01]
gen/manuf/fdm/new/lennart/MagToolChanger_Lockplate_part1_1.stl
14.0 x 37.8 x 32.8

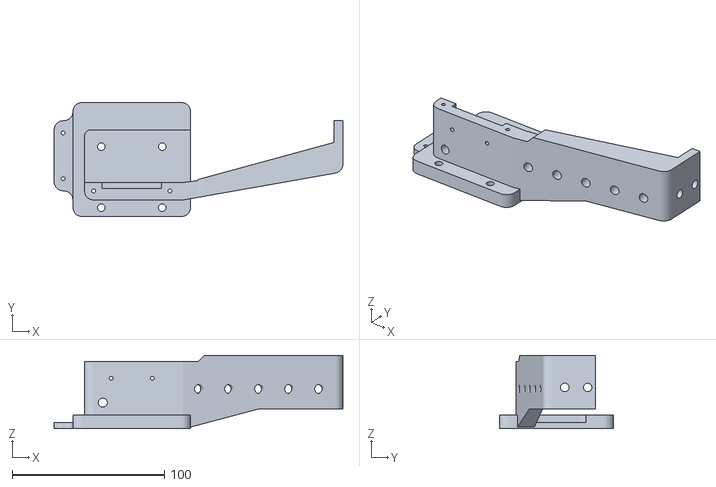
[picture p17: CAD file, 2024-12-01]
gen/manuf/fdm/new_2024/Mag_Tool_Changer_Baseplate.stl
189.5 x 74.8 x 48.0

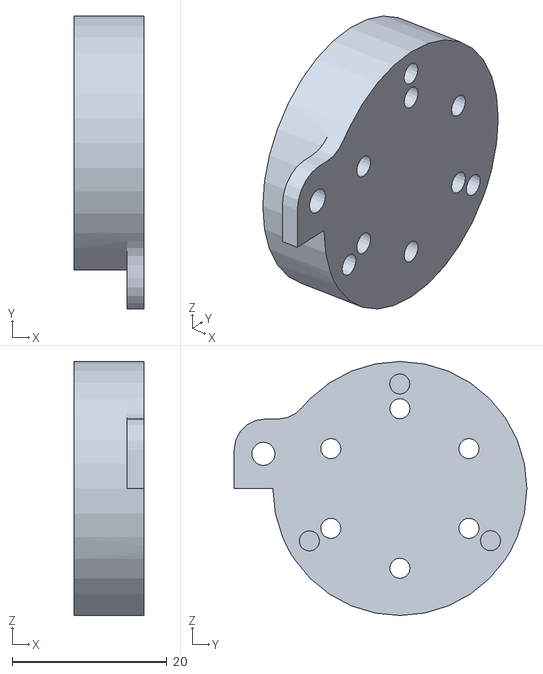
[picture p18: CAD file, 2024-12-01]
gen/manuf/fdm/MagToolChanger_Lockplate_part1.stl
9.00 x 37.8 x 32.8

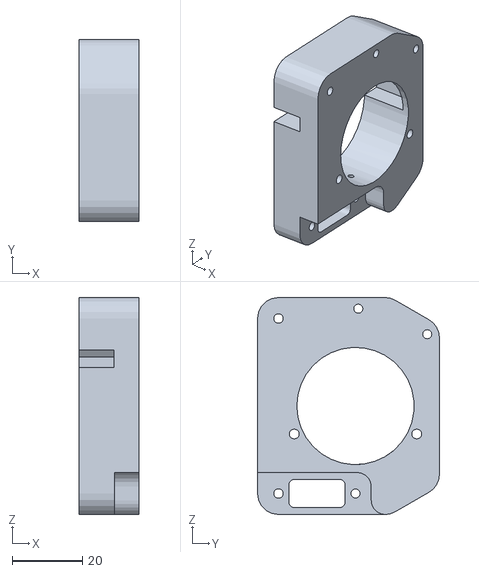
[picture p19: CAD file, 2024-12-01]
gen/manuf/fdm/new/lennart/MagToolChanger_HeadBase_2.stl
17.0 x 52.0 x 62.0

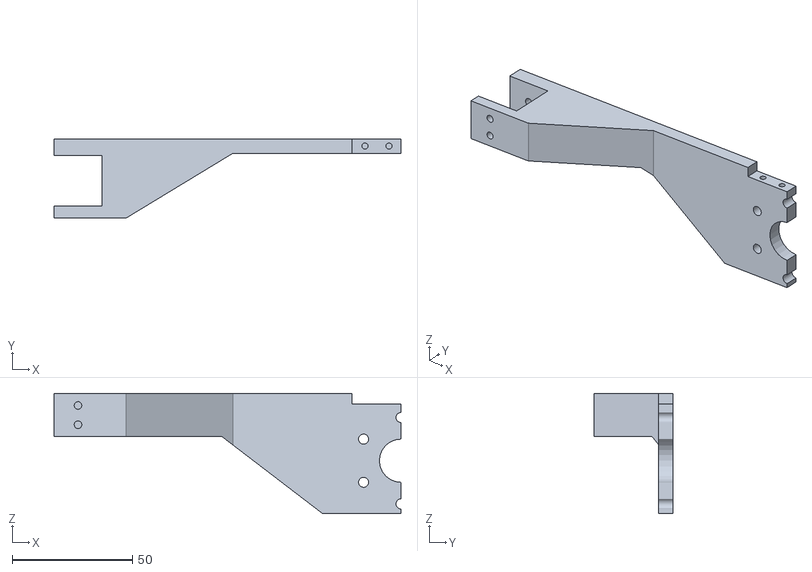
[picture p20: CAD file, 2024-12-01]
gen/manuf/fdm/new/mounting_storage_p2.stl
144.5 x 33.0 x 50.0

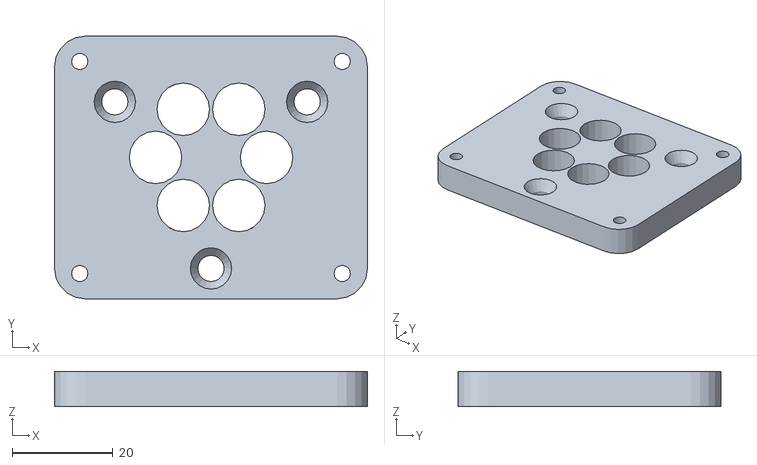
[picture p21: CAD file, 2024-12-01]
gen/manuf/fdm/new_2024/plate_tool_board_1.stl
62.0 x 52.0 x 7.00

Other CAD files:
gen/manuf/fdm/new/lennart/inner_housing_separator_4.stl
gen/manuf/fdm/new_2024/spacer_storage_mounting.stl
gen/manuf/fdm/new/lennart/Mag_Tool_Changer_Baseplate.stl
gen/manuf/fdm/new/plate_tool_board.stl
doc/bom/tool-changer_system_tcs/tcs_assbl_dwg1_bom.prt
gen/manuf/fdm/MagToolChanger_HeadBase.stl
gen/manuf/fdm/MagToolChanger_HeadBase_2.stl
gen/manuf/fdm/MagToolChanger_Lockplate_part1_1.stl
gen/manuf/fdm/MagToolChanger_Lockplate_part2.stl
gen/manuf/fdm/MagToolChanger_Lockplate_part2_1.stl
gen/manuf/fdm/Mag_Tool_Changer_Baseplate_1.stl
gen/manuf/fdm/Mag_Tool_Changer_Baseplate_2.stl
gen/manuf/fdm/Mag_Tool_Changer_Baseplate_3.stl
gen/manuf/fdm/inner_housing_separator.stl
gen/manuf/fdm/mounting_storage_p1.stl
gen/manuf/fdm/new/dummy_piston.stl
gen/manuf/fdm/new/lennart/MagToolChanger_HeadBase.stl
gen/manuf/fdm/new/lennart/MagToolChanger_HeadBase_1.stl
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

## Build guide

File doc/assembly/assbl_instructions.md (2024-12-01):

# OSHOP Electronics Testing Module (OSH Demonstrator) Assembly Instructions

[TOC]

## Assembly Module Structure

[bom sts](worktree\development_osh\src\mech\structure-system_sts\sts_bom.pdf)

- remark: the module structure is assembled by using aluminium profiles and dedicated automatic connectors
- the first picture shows one of this connectors integrated in the assembly points
- points where new connectors must be added are marked with red dots in the pictures
- keep in mind to first insert the screws in the slot, because this is not possible after assembling the other components of the automatic connector

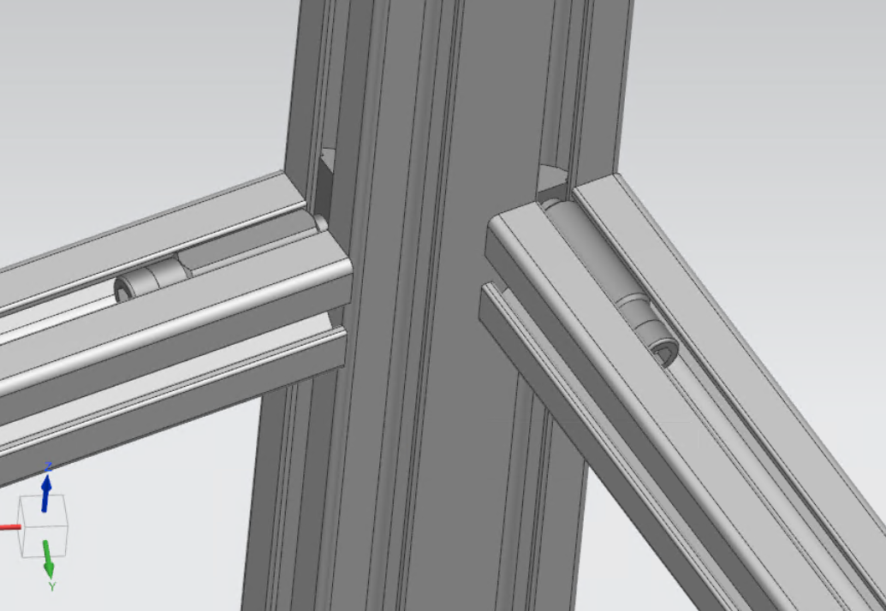
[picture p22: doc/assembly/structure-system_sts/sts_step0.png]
TCS Assembly Step 1


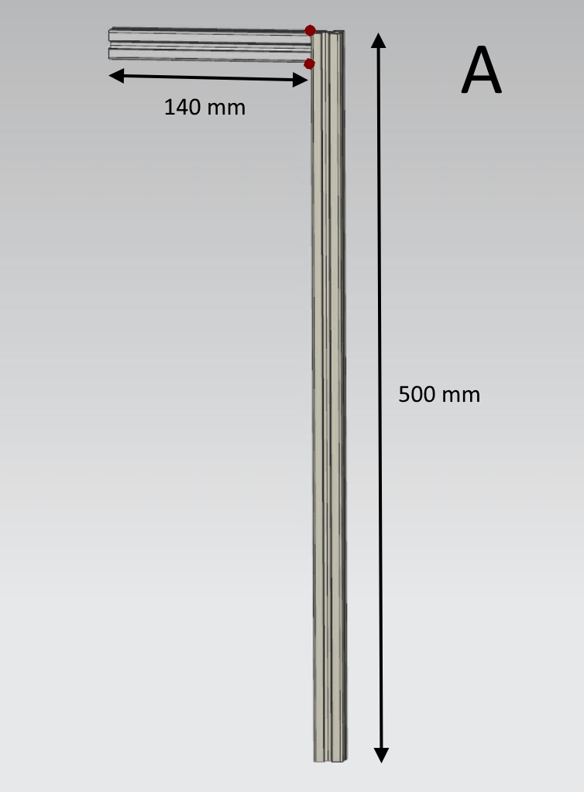
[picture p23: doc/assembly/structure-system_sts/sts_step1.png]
TCS Assembly Step 1


- Assemble group A by joining the two 20x20 profiles

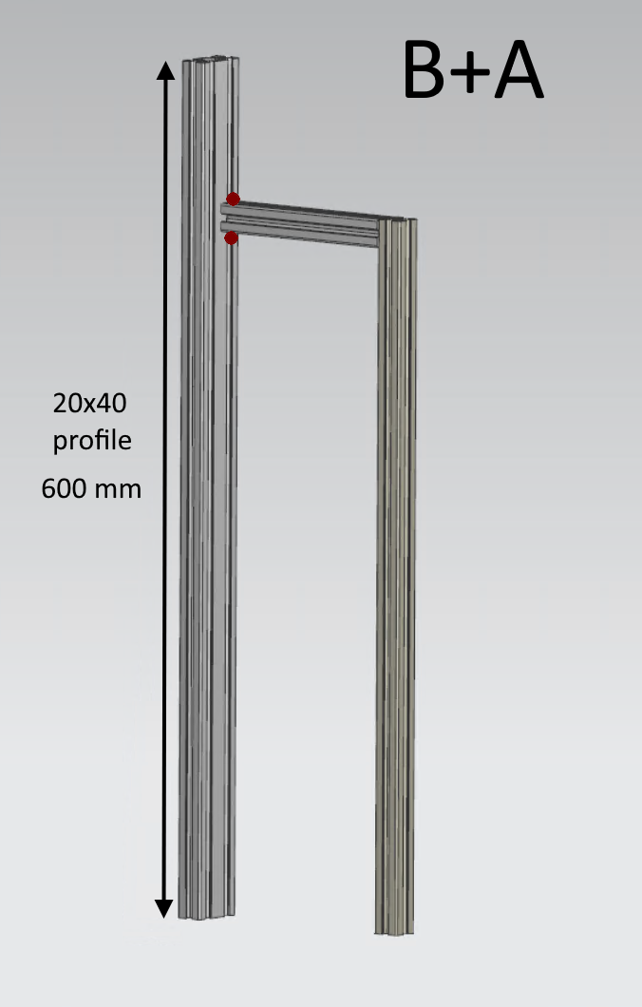
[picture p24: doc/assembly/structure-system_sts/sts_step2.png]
TCS Assembly Step 1


- Merge group A to a 20x40 profile to obtain group B+A

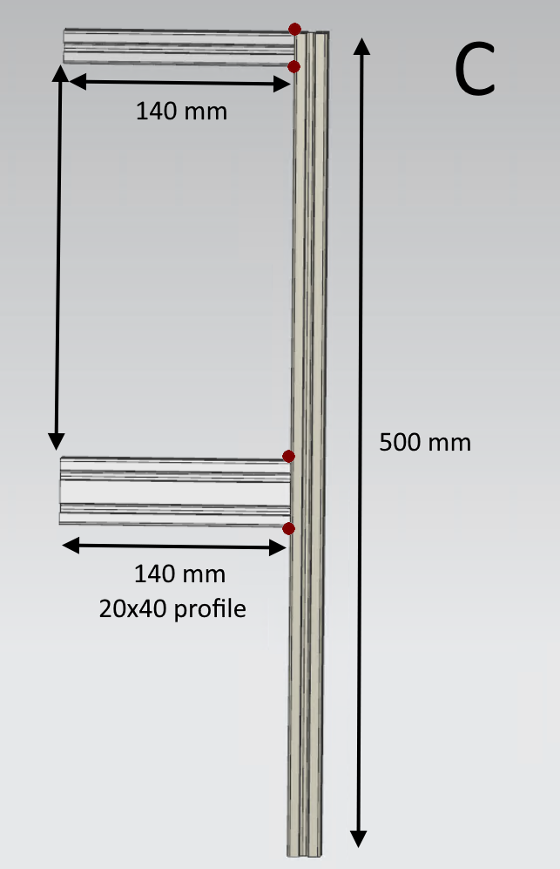
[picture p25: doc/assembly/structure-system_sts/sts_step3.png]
TCS Assembly Step 1


- Assemble group C by joining the 3 profiles shown in the picture above

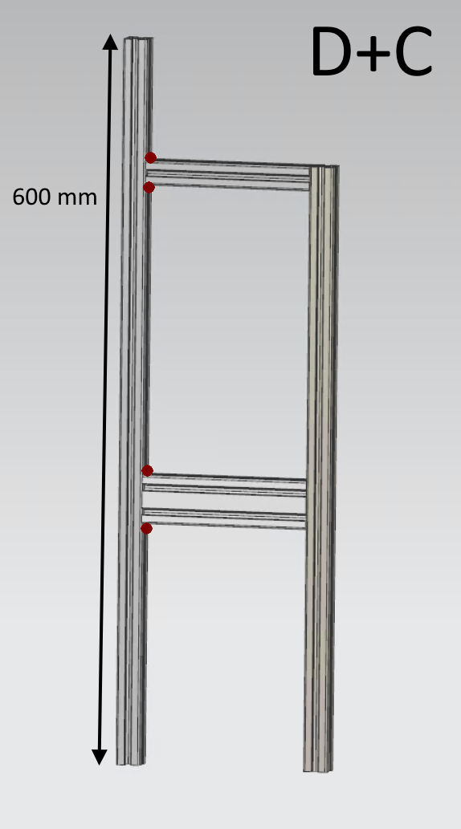
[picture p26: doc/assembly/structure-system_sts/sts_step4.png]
TCS Assembly Step 1


- Merge group C to a 20x20 profile (length 600 mm) to obtain group D+C

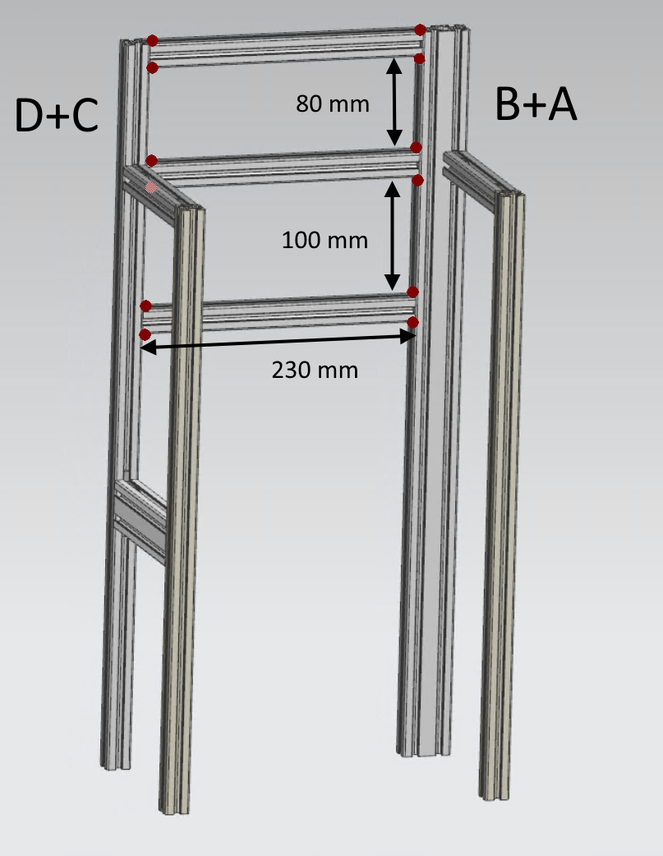
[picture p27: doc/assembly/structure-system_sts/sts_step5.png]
TCS Assembly Step 1


- Connect group D+C and group B+A using 3 20x20 profiles (length 230 mm)
- Set up the spacing between the profiles like illustrated in the picture

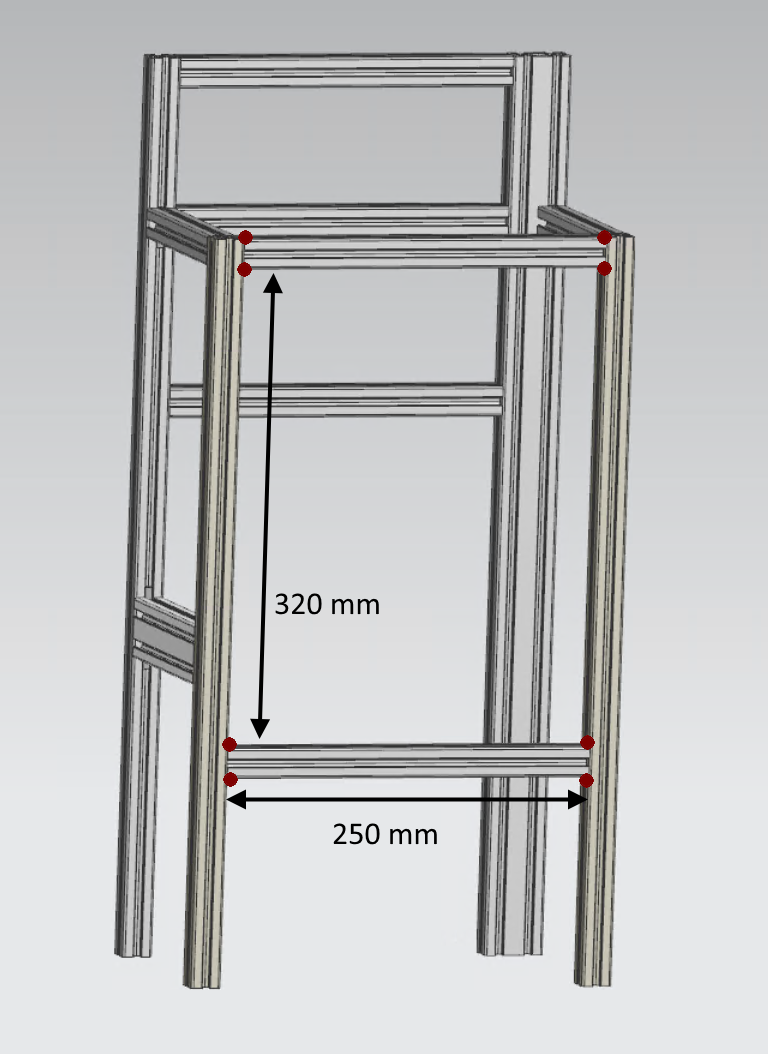
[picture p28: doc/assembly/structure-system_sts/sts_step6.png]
TCS Assembly Step 1


- Add 2x 20x20 profiles (length 250 mm) to achieve better stiffness

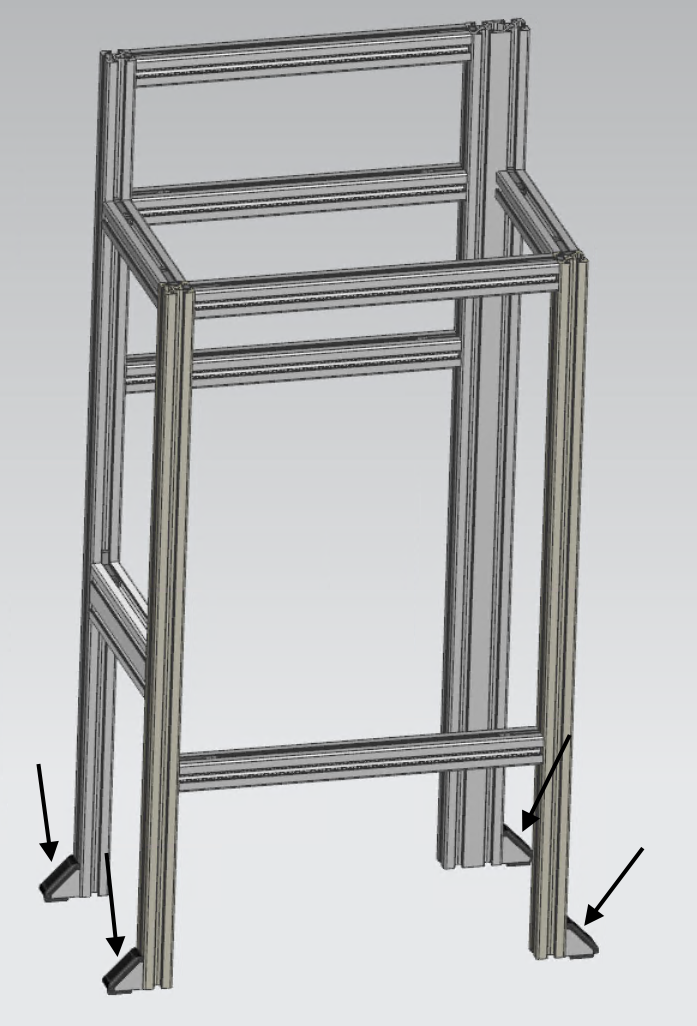
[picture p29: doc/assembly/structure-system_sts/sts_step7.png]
TCS Assembly Step 1


-Add 4x brackets for connection with the mechanical interface later on

## Assembly Linear Guide

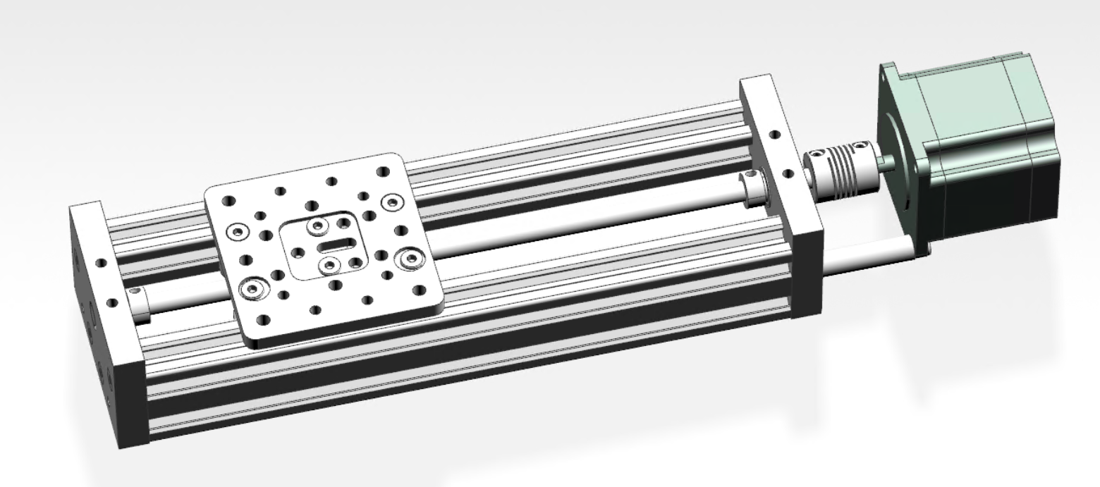
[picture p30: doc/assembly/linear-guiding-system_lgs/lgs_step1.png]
TCS Assembly Step 1


- full assembly of available open builds parts store guiding system should look like this
- link to store: https://us.openbuilds.com/c-beam-linear-actuator-bundle/

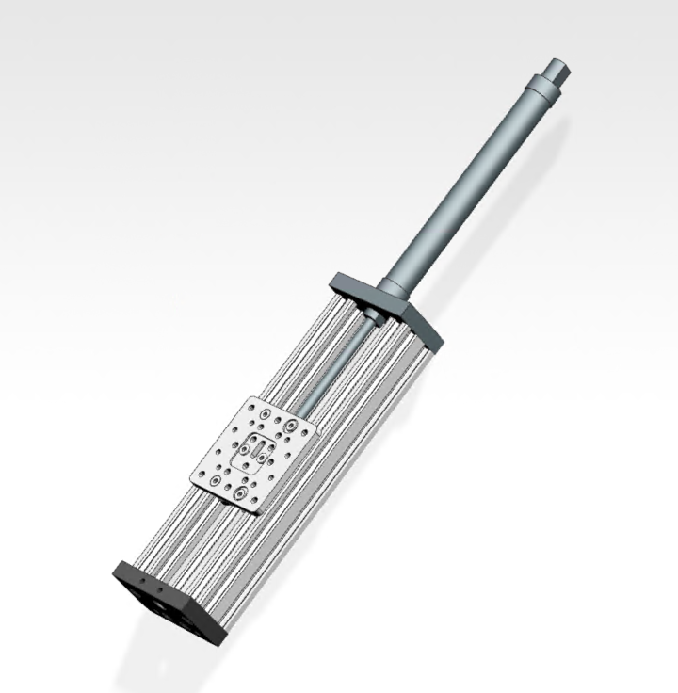
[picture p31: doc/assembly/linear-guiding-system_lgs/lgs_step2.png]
TCS Assembly Step 1


- remove the spindle, bearings etc.
- replace the topplate with `guiding-piston-plate_lgs` and screw in the piston
- connect the piston rod with the sledge
- keep in mind to utilize piston with sufficient piston stroke

## Assembly Tool Changing System

[bom tcs](worktree\development_osh\src\mech\tool-changer-system_tcs\tcs__bom.pdf)

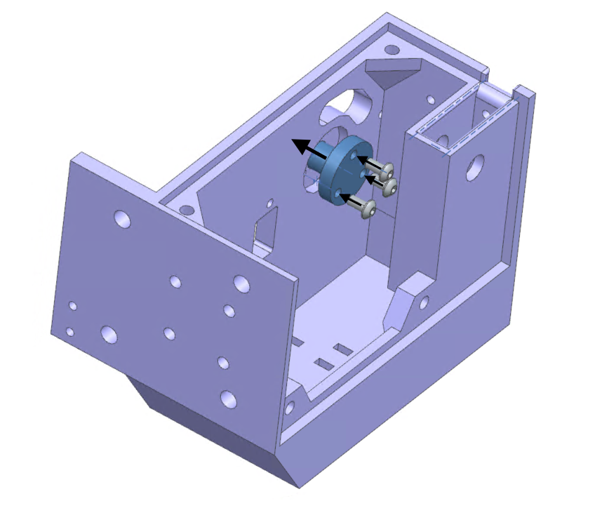
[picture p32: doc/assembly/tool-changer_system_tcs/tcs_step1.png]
TCS Assembly Step 1


- Insert `head-shaft_tcs` into `baseplate_tcs` and tightening with 3x socket button head ISO 7380 m3x6 screws

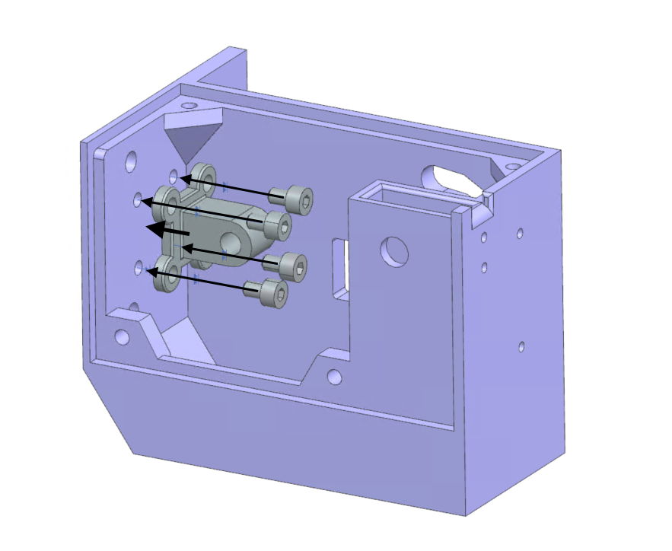
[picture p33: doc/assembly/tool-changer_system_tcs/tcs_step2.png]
TCS Assembly Step 2


- Secure the piston adapter
- We used the accessory components to FESTO `ADVL 10-10 APA` and 4x socket head screws ISO 4762 m4x6.

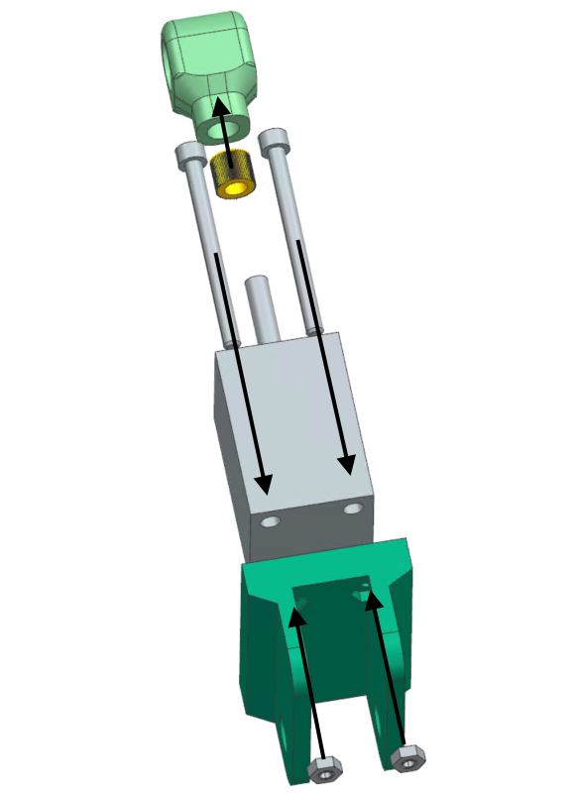
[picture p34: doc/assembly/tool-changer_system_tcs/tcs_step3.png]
TCS Assembly Step 3


- Insert a heated m4 thread insert into `piston-head_tcs` (we used a soldering iron to heat the insert)
- Join `piston-mount-b_tcs` and the piston by using 2x socket head cap DIN 4762 m3x36 screws and 2x hex nut ISO 4032 m3
- We used FESTO `ADVL 10-10 APA` piston

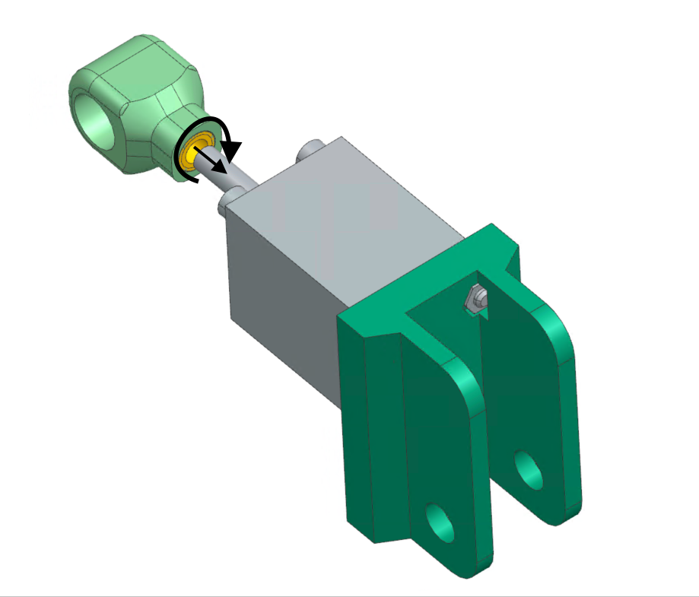
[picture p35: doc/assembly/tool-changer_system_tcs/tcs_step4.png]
TCS Assembly Step 4


- Tightening the piston head to the shaft of the piston

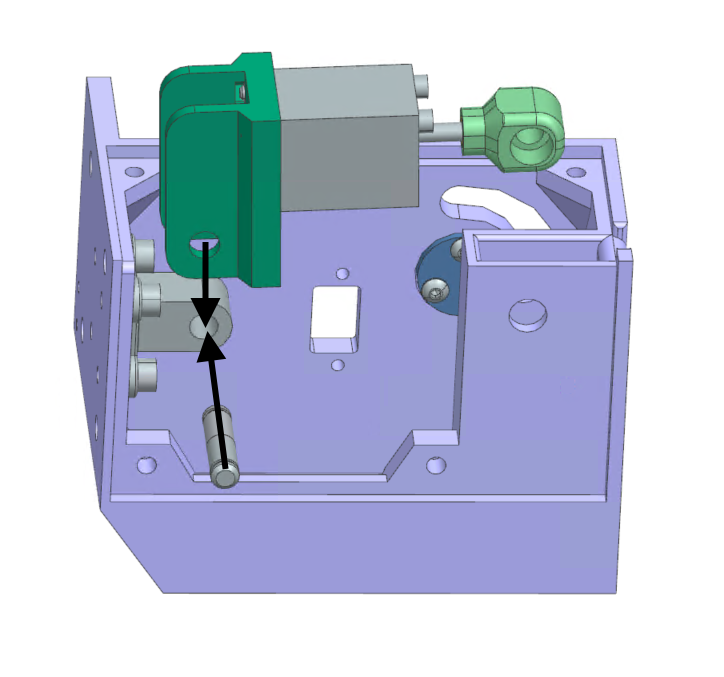
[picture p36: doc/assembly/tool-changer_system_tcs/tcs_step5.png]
TCS Assembly Step 5


- Join the piston adapter and `piston-mount-b_tcs`
- Secure with the piston mount shaft

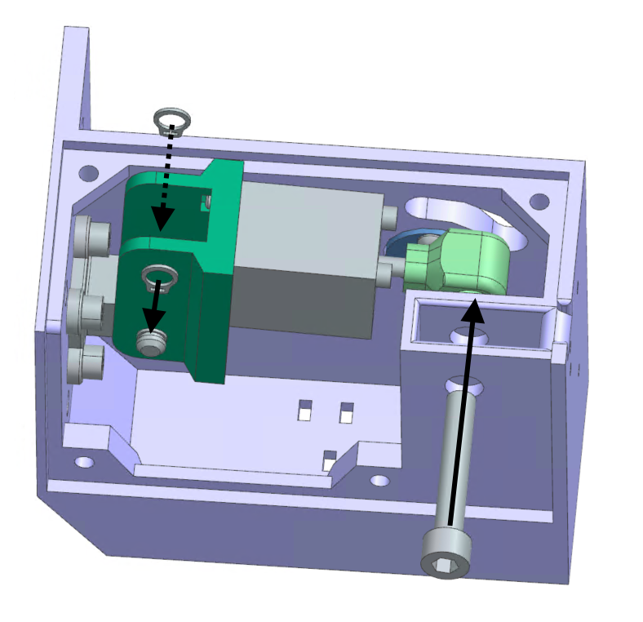
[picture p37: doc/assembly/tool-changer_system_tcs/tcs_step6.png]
TCS Assembly Step 6


- Add circlip for shafts DIN 471 6x0p7 on each side to secure the piston mount shaft
- Insert a socket head cap screw DIN 4762 m5x30 into the `piston_head_tcs`

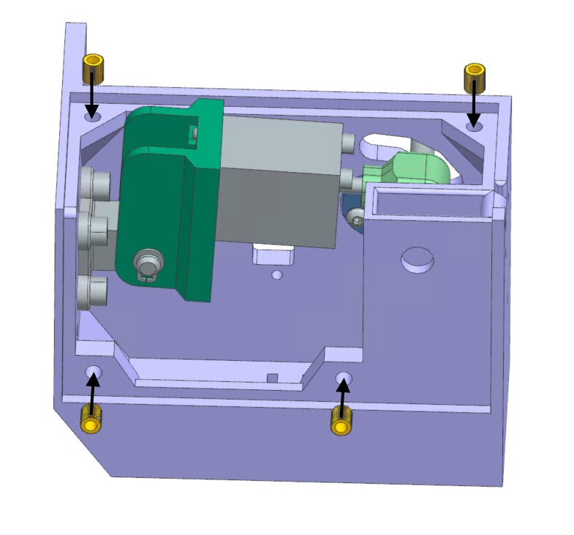
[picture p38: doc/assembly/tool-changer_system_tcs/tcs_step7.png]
TCS Assembly Step 7


- Insert 4x heated m3 thread inserts into the `baseplate_tcs` (for example by using a soldering iron)
- This step is optional 
- Only do this assembly if you plan to cover the TCS actuation mechanism using the `cover_tcs`

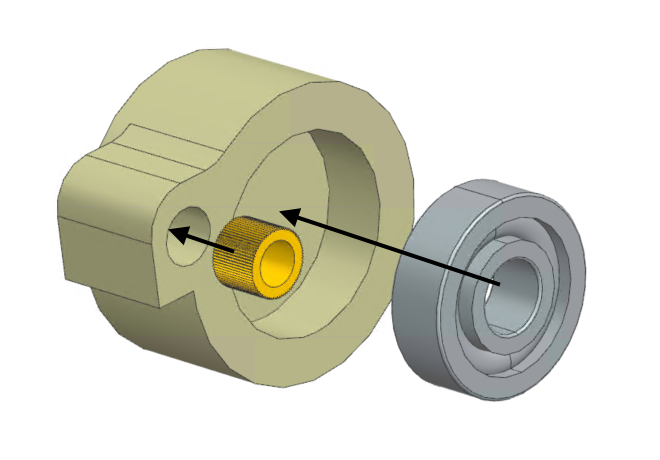
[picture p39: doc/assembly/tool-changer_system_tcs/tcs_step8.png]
TCS Assembly Step 8


- Insert 1x m5 thread insert into the `lockplate_tcs` (for example by using a soldering iron)
- Press the radial ball bearing DIN 625-608 into the `lockplate_tcs`

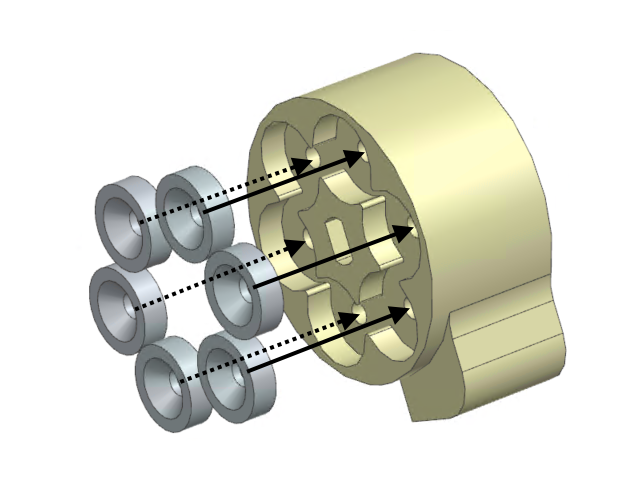
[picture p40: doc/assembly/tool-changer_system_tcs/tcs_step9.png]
TCS Assembly Step 9


- Press 6x countersunk magnet into the `lockplate_tcs`
- Optional step (recommended): Secure the countersunk magnets with 6x socket countersunk head screw DIN 7991 m3x8

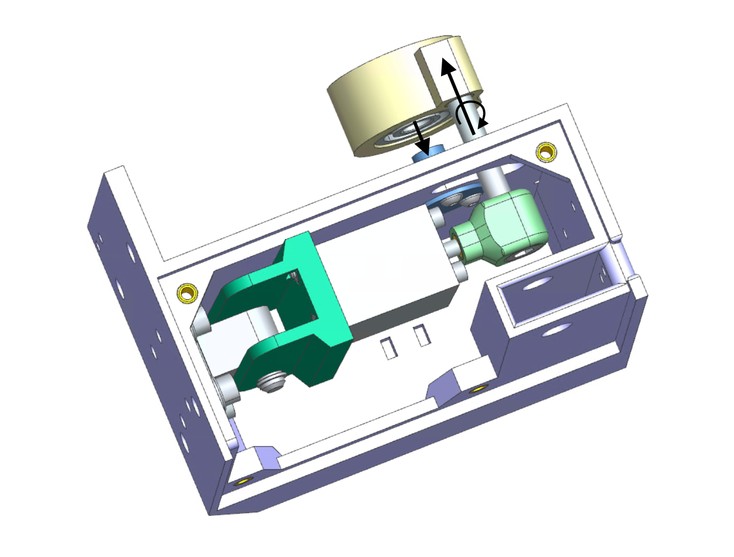
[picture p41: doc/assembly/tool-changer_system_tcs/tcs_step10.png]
TCS Assembly Step 10


- Fit the bearing assembled to the `lockplate_tcs` on the `head-shaft_tcs`
- Connect the piston and the `lockplate_tcs` by screwing in the socket head cap screw DIN 4762 m5x30

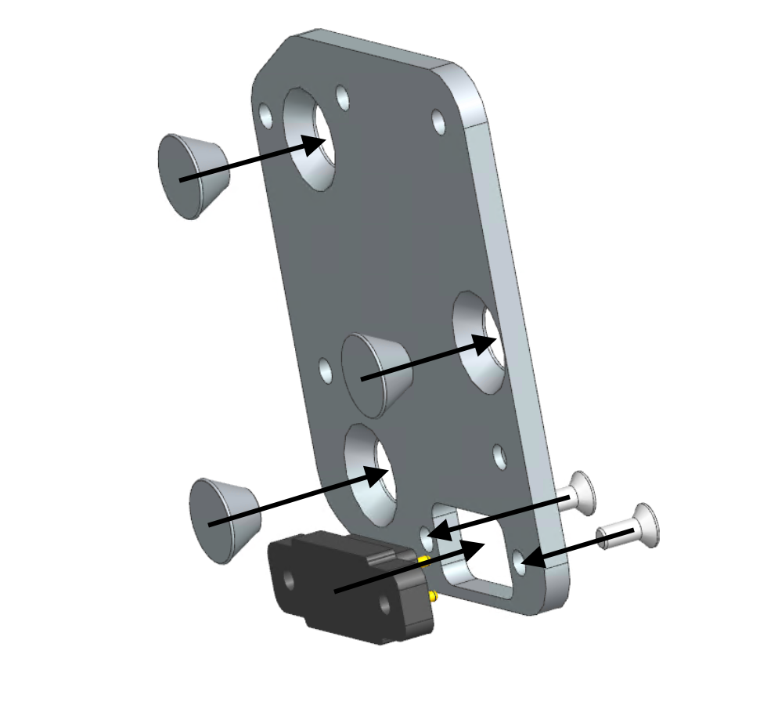
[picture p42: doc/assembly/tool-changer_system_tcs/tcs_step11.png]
TCS Assembly Step 11


- Tightening the signal connect side A to the `head-plate_tcs` using 2x hex socket countersunk flat head DIN 7991 m2.5x6 screws
- Put the 3x conical magnets in the countersunk located at the bottom side of the `head-plate_tcs`

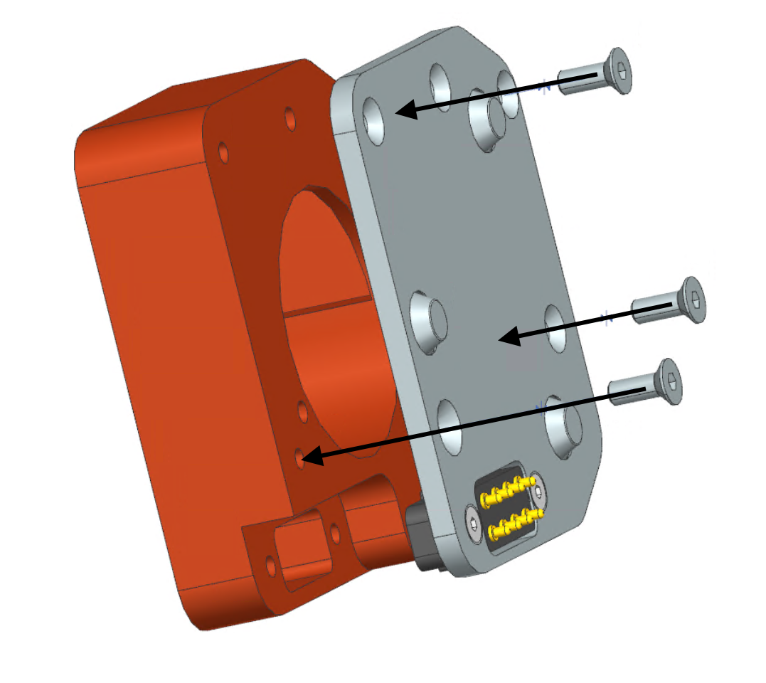
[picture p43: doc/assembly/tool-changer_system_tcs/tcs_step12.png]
TCS Assembly Step 12


- Mount the `head-plate_tcs` to the `head-base_tcs` using 3x socket countersunk head screw DIN 7991 m3x8
- Recommendation: Slide the `head-plate_tcs` on the `head-base_tcs` (sideways) in order to avoid dropping the inserted conical magnets
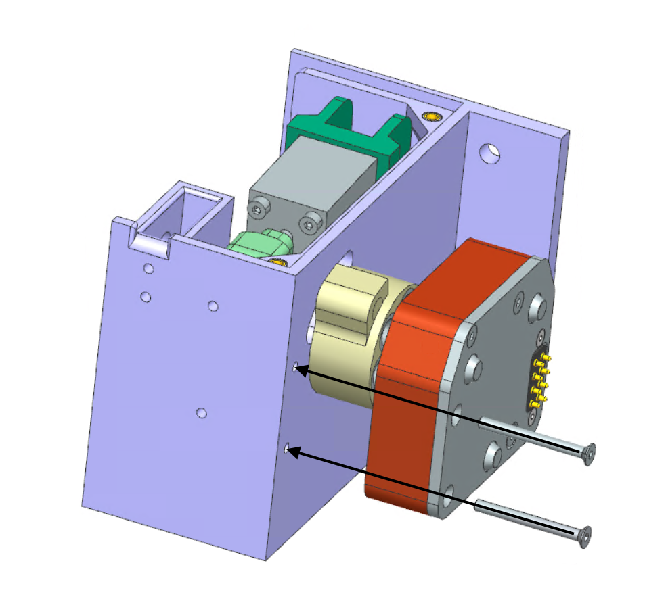
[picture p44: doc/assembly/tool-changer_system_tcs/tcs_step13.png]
TCS Assembly Step 13


- Attach the previous assembled parts to the `baseplate_tcs` using 2x socket countersunk head screws DIN 7991 m3x30
- Recommendation: Apply grease to the contact surfaces between the `lockplate_tcs` and the `head-base_tcs`

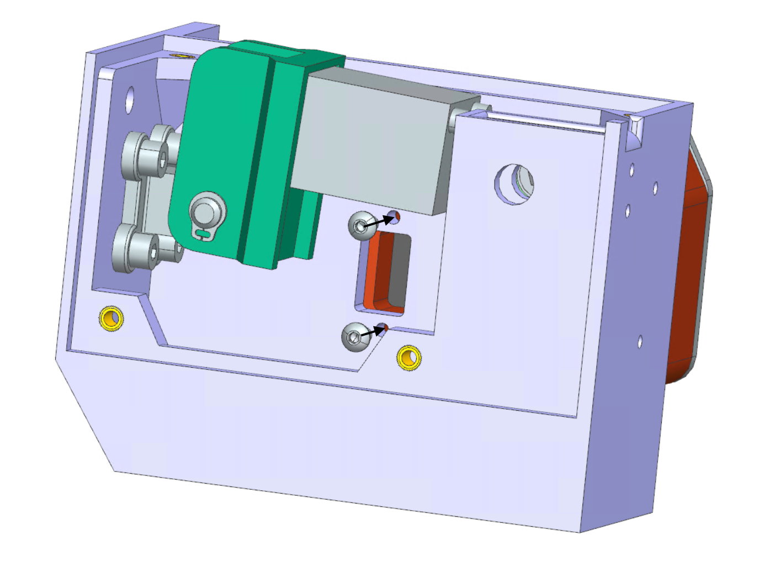
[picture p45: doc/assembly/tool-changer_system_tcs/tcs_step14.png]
TCS Assembly Step 14


-Secure the changer head from the opposite site by screwing in 2x socket button head screw ISO 7380 m3x10

## Assembly Tool Storage System

[bom tss](worktree\development_osh\src\mech\tool-storage-system_tss\tss_bom.pdf)

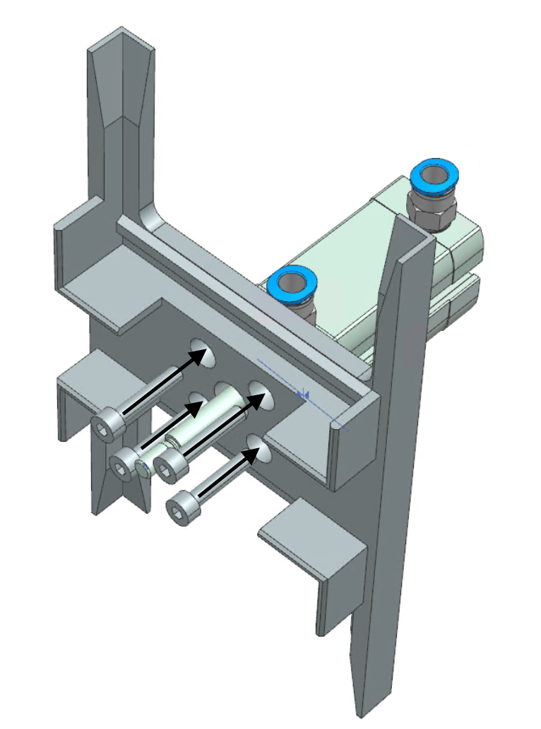
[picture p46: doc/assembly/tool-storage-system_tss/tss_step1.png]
TSS Assembly Step 1


- Attach the piston to the `storage-body-a_tss` using 4x socket head cap screw DIN 472 m4x20
- The pneumatic connectors of the piston shall point in the illustrated direction
- We used FESTO `ADN 16-20 APA` piston

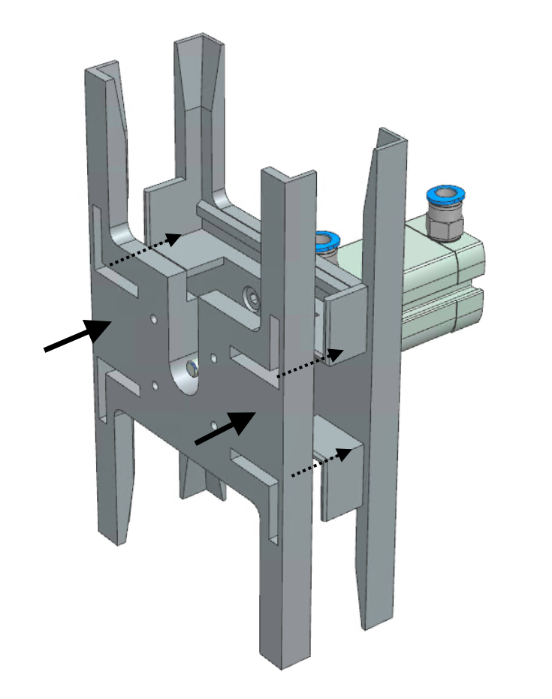
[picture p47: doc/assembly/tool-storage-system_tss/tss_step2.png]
TSS Assembly Step 1


- Slide the `storage-body-b_tss` on the L-shaped connectors of `storage-body-a_tss`

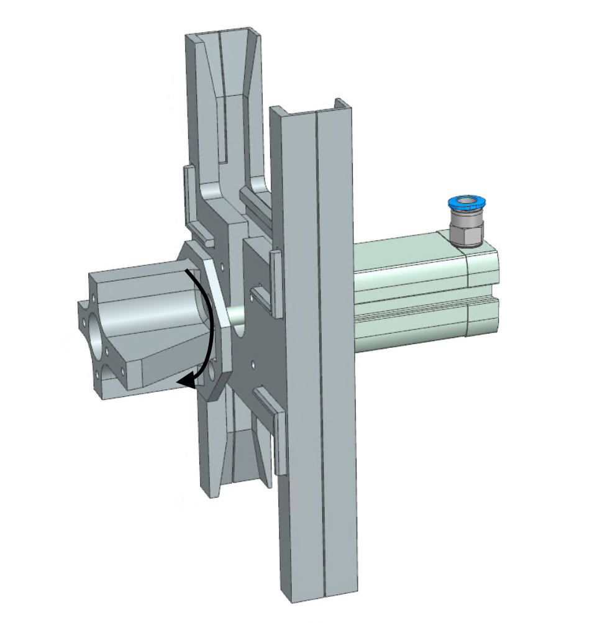
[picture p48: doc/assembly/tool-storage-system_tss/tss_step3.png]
TSS Assembly Step 1


- Tightening the `spacer_tss` on the thread of the piston rod
- Avoid spinning of the rod by holding it with a pliers like shown in the next picture to avoid 

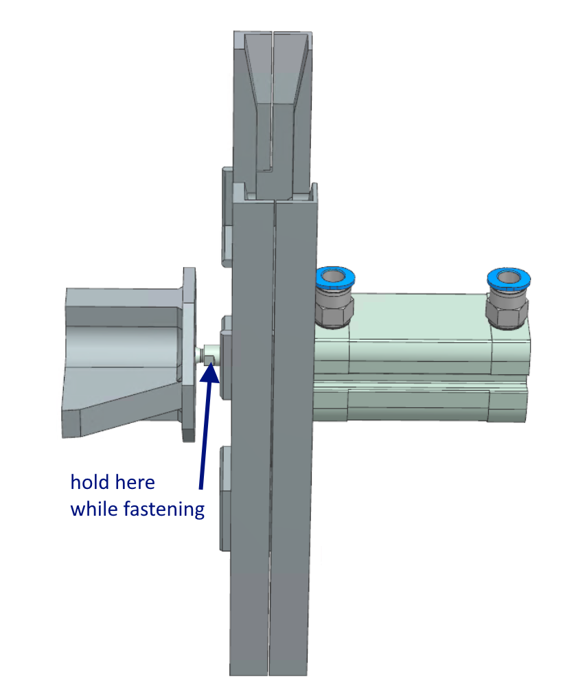
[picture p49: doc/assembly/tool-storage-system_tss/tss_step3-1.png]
TSS Assembly Step 1


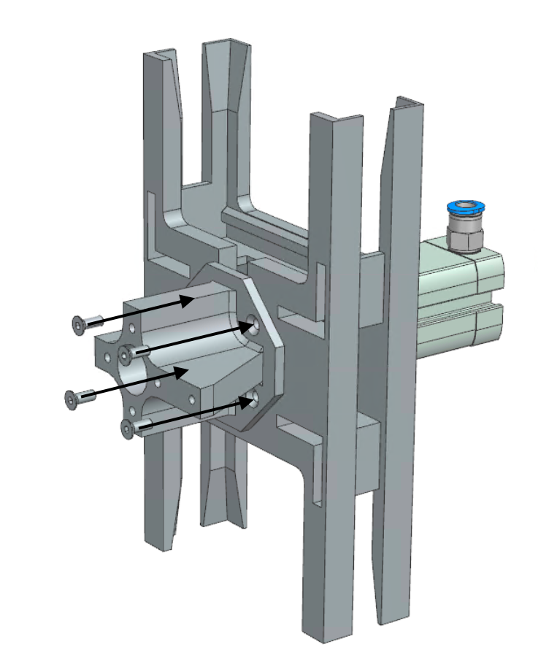
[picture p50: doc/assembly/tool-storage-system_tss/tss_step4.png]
TSS Assembly Step 1


- Secure the `spacer_tss` with 4x socket countersunk head screws DIN 7991 m3x8

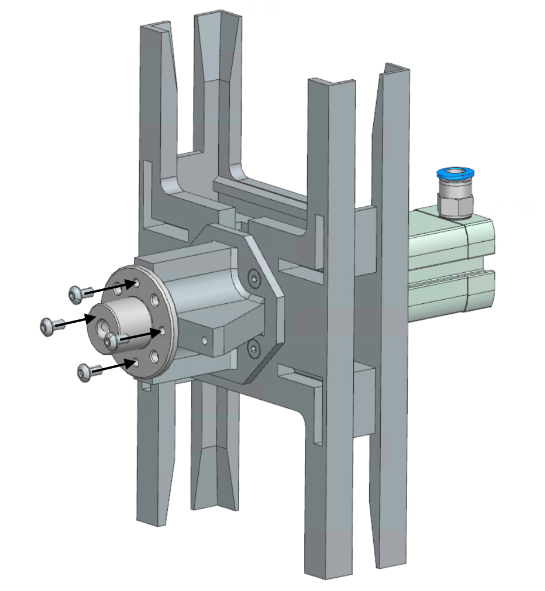
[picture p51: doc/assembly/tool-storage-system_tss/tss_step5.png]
TSS Assembly Step 1


- Attach the adapter of the rotational piston to the `spacer_tss` by screwing in 4x socket button head screws ISO 7380 m3x6
- We used the piston FESTO `DRVS 12 180P` and the coresponding acessories

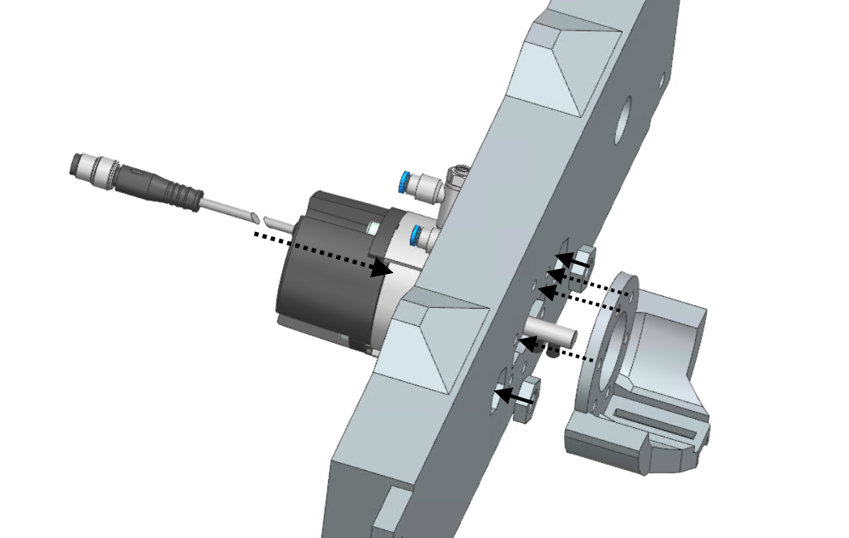
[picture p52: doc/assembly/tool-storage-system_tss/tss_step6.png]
TSS Assembly Step 1


- Insert 2x hex thin nut ISO 4036 m8 in the `mounting_tss`
- Put the rotational piston and the `sensor_flange_tss` in place

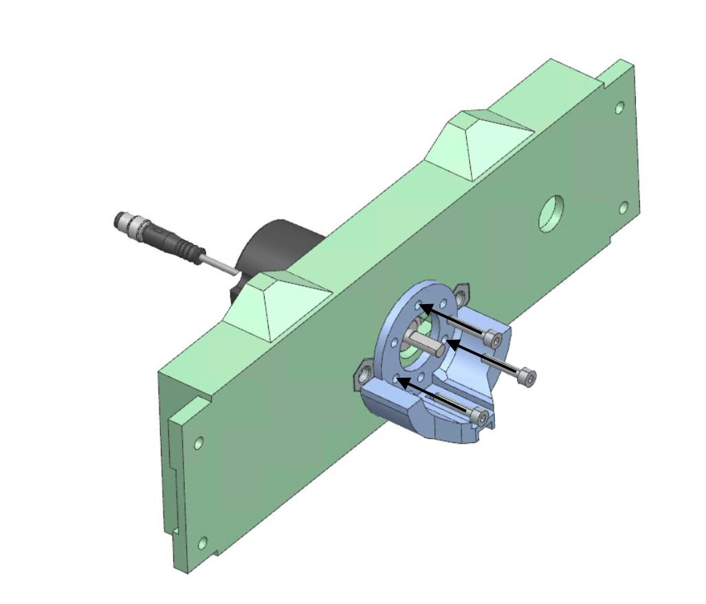
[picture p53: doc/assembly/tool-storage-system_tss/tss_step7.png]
TSS Assembly Step 1


- Secure the rotational piston and the `sensor_flange_tss` using 3x socket head cap screw DIN 4762 m4x20

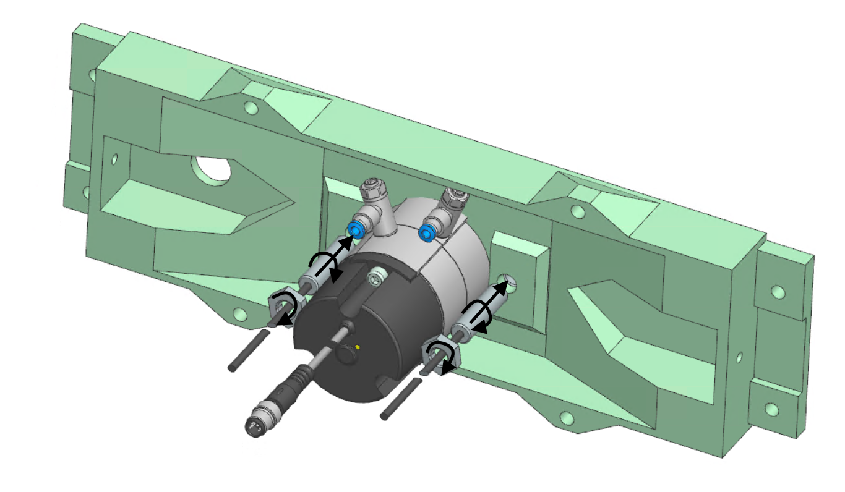
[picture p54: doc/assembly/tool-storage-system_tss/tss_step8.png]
TSS Assembly Step 1


- Screw the two inductive sensor m8 into the assemble hex nuts and secure them with another set of hex thin nut ISO 4036 m8

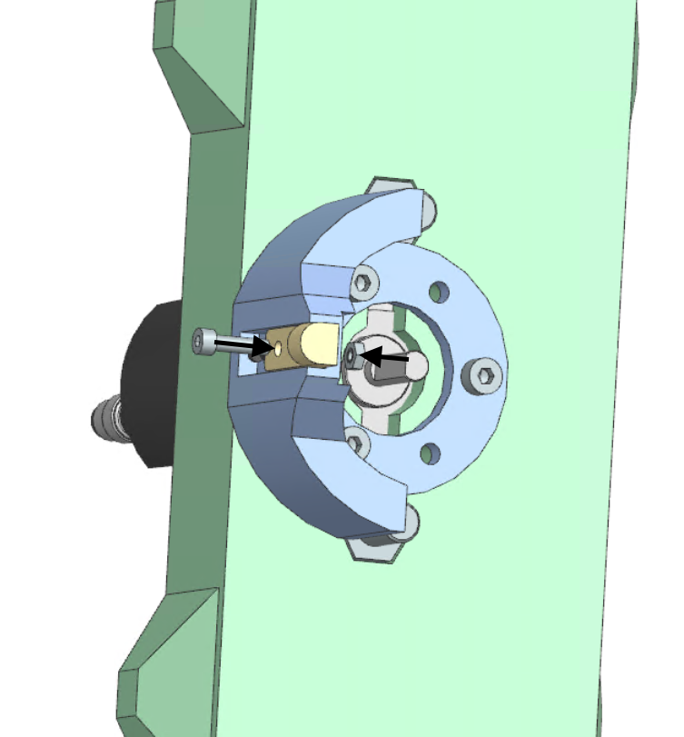
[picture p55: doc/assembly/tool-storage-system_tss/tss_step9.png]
TSS Assembly Step 1


- Add the inductive tool sensor to the `sensor_flange_tss` using a socket head cap screw DIN 4762 m3x12 and a hex nut ISO 4032 m3

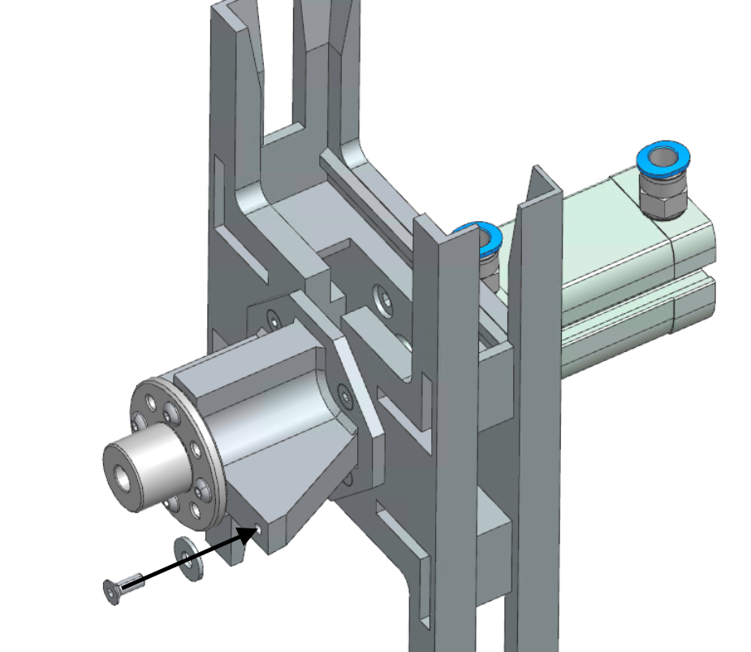
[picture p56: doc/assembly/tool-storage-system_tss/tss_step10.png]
TSS Assembly Step 1


- Assemble the counterpart of the tool inductive sensor by joining a plain washer type ab DIN 6903 m4 using a socket countersunk head screw DIN 7991 m3x8

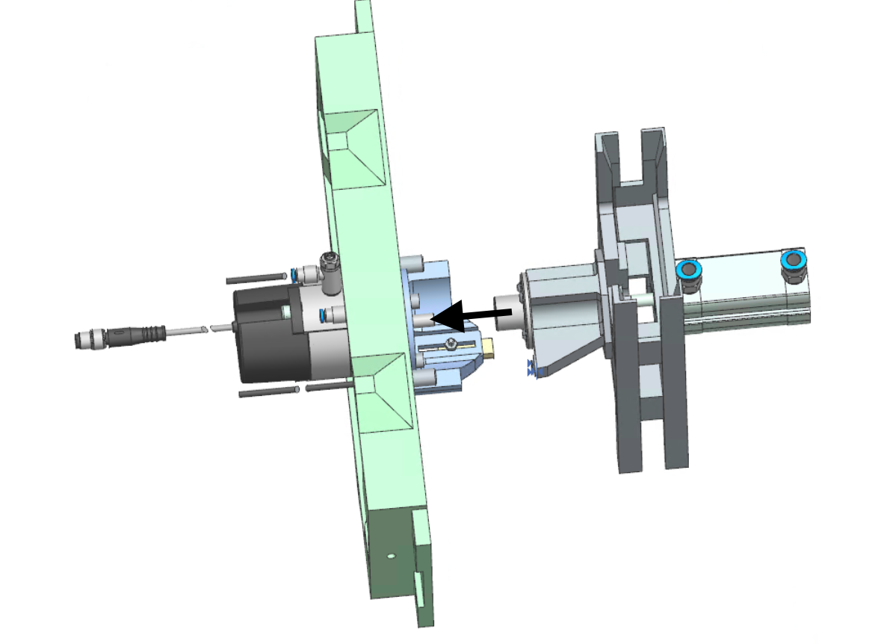
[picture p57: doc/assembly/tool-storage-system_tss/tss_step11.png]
TSS Assembly Step 1


- Put the piston adapter on the rotational piston rod

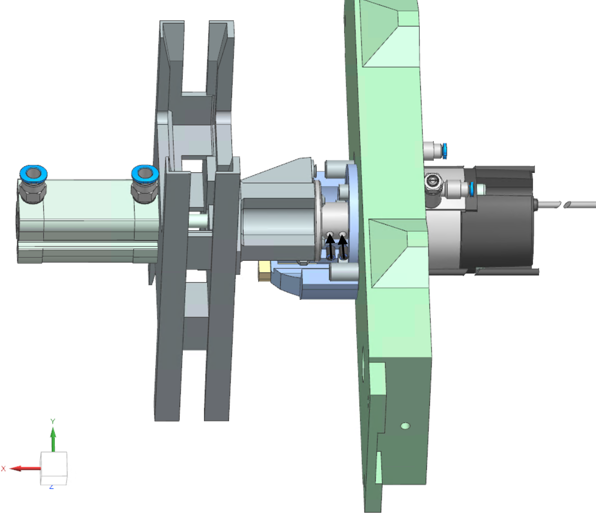
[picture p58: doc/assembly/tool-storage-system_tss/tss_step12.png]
TSS Assembly Step 1


- Secure the adapter using 2x allen screws DIN 913 m4x6

## Assembly Chang-E

[bom Chang-E](worktree\development_osh\src\mech\Chang-E_bom.pdf)

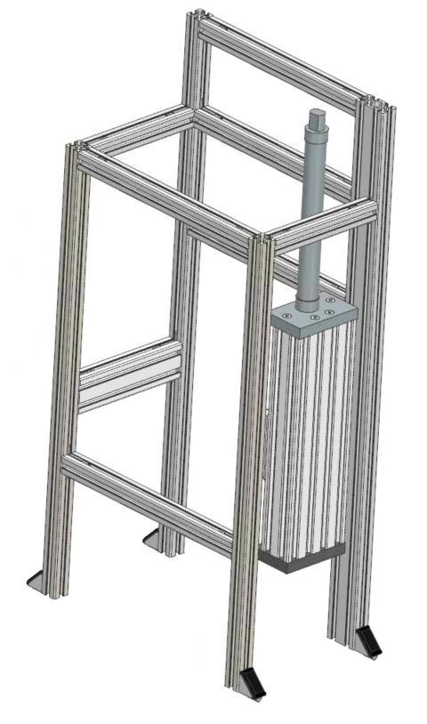
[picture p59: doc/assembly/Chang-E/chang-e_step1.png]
TSS Assembly Step 1


- Join the linear guiding system and the structure e.g. by using slot nuts, brackets and matching screws
- choose sufficient spacing between the bottom plane of the structure and the bottom of the linear guide, in order to reach target operation position with the tools later on

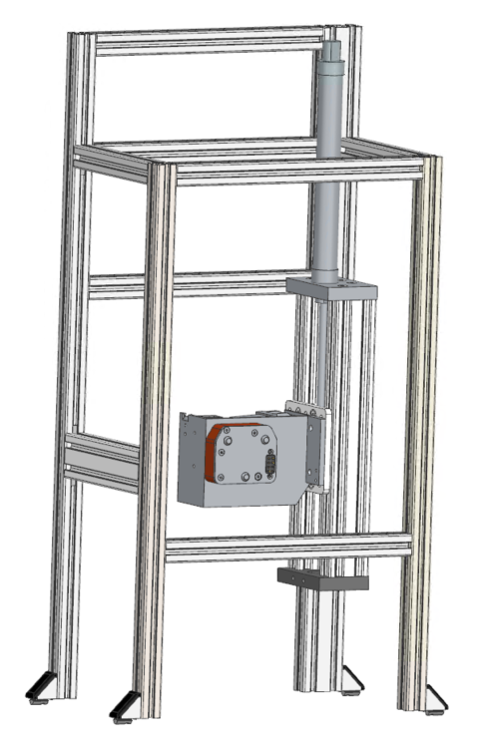
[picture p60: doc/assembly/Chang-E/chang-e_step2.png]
TSS Assembly Step 1


- Mount the tool changing system to the sledge of the linear guide using matching screws and the threads offered by the sledge

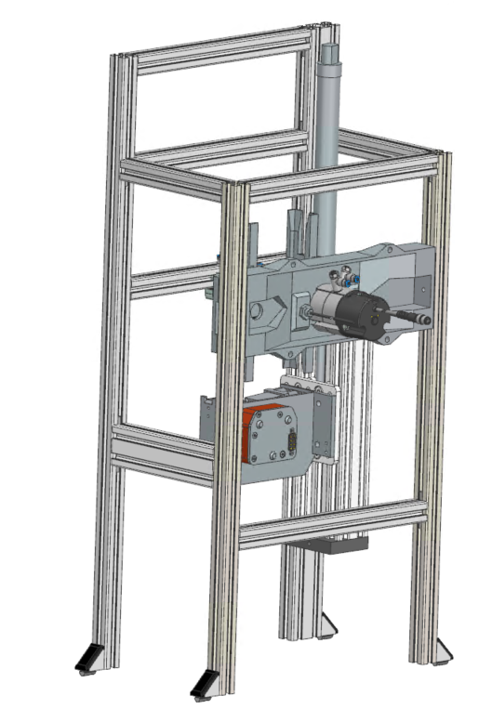
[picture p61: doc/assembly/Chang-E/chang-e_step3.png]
TSS Assembly Step 1


- Mount the tool storage system to the structure e.g. by using slots nots and matching screws
- Adapt the position of the tool storage system to the maximum position of the sledge

TSS Assembly Step 1

- Add tools to the storage and the tool changer coupler

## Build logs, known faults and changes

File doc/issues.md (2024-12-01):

# Documentation

## TODOS:

- [ ] BOM erstellen
- [ ] Auslagerung der Teilbaugruppen in separate Repositories
- [ ] Nachmodellierung proprietärer Modelle, welche nicht veröffentlicht werden dürfen
- [ ] Schaltpläne
    - Elektronik
    - Pneumatik
- [ ] Flussdiagramm über Funktionsprinzip der Maschine
- [ ] Dokumentation
    - Visualisierungen:
        - der einzelnen Schritte
        - der gesamten Maschine
    - Aufbauanleitung

## Probleme/Herausforderungen

- Konstruktion
    - Nicht alle Komponenten im CAD modelliert
        - Steuerungsmodule und Anschlüsse fehlen
        - Kabel und Schläuche fehlen
        - Schraubverbindungen sind nicht modelliert
        - Montierbarkeit bestimmter Teile dadurch schwierig
        - automatische Generierung einer BOM nur sehr eingeschränkt möglich
            - erfordert manuelles abgleichen des physischen Prototyps

- Kollaboration:
    - inkonsistentes Benennen der Dateien
    - Benennung/Beschreibung teilweise doppeldeutig
    - Umbenennen im Dateibrowser führt zu Zuordnungsproblemen im CAD

- Dokumentation
    - nachverfolgen der Änderungen nur manuell möglich, da keine Visualisierung der Veränderungen der CAD-Modelle zwischen den Commits möglich ist
        - Vergleich nur in NX möglich mittels `Compare Body`
        - setzt voraus zwei Commits vollständig auschecken zu müssen

- Programmierung:
    - Programmierung der Ansteuerung erfolgt über Tablet (IPad) mit Festo Software (Tec2Screen/iEasyLab)
        - Modellierungssprache: Festo iEasyLab, Lua
        - Entwicklungsstände der Festosoftware erfolgen entkoppelt von Konstruktion im Repository
        - Doku bisher nicht vorhanden oder auffindbar, bzw. zu einfach
        - bietet `Lua`-Schnittstelle, allerdings nicht gut dokumentiert
            - Programmierung per Touch/Softtastatur auf dem Tablet sehr unkomfortabel
            - keine "moderne" IDE, kein Syntaxhighlighting, Linting, etc.
            - `iEasyLab` bietet keine Programmiertastatur an
        - Export des Modells möglich zu `.ieasylab`-Datei
            - Datei ist XML-basiert, Zeilenvergleich möglich
            - Export und Import allerdings nur manuell möglich
            - Übertragung in Repository nur manuell per Bluetooth/WLAN möglich
                - Gefahr, dass Entwicklungsstände in Commits vergessen werden
        - Programmierung mittels iEasyLab und Lua nicht möglich, da ein getimter Ablauf, mittels Waits durch ein Execution-Timeout unterbrochen wird
        - Dokumentation nicht mehr online verfügbar (nicht von Festo angeboten)
    - Tests müssen manuell ausgeführt werden
        - evtl. Möglichkeit `Lua`-Skripte in einer Testumgebung auf dem Rechner zu entwickeln

## Designfragen

- Pneumatik
    - einfachere Ansteuerung (1|0)
        - aber u.U. mehr Sonsorik nötig zur Zustandserfassung
    - Demonstrator ist als Erweiterung des Festo-Moduls konzipiert
        - Festo-Modul (CPFactory) bietet umfangreiche Anschlüsse und Entwicklungsbasis
        - Portabilität auf andere Systeme ggf. schwierig
- Gehäuse
    - bis jetzt nicht vorgesehen
- Montage
    - 3D-Druckteile werden mittels Thermoplastschrauben montiert

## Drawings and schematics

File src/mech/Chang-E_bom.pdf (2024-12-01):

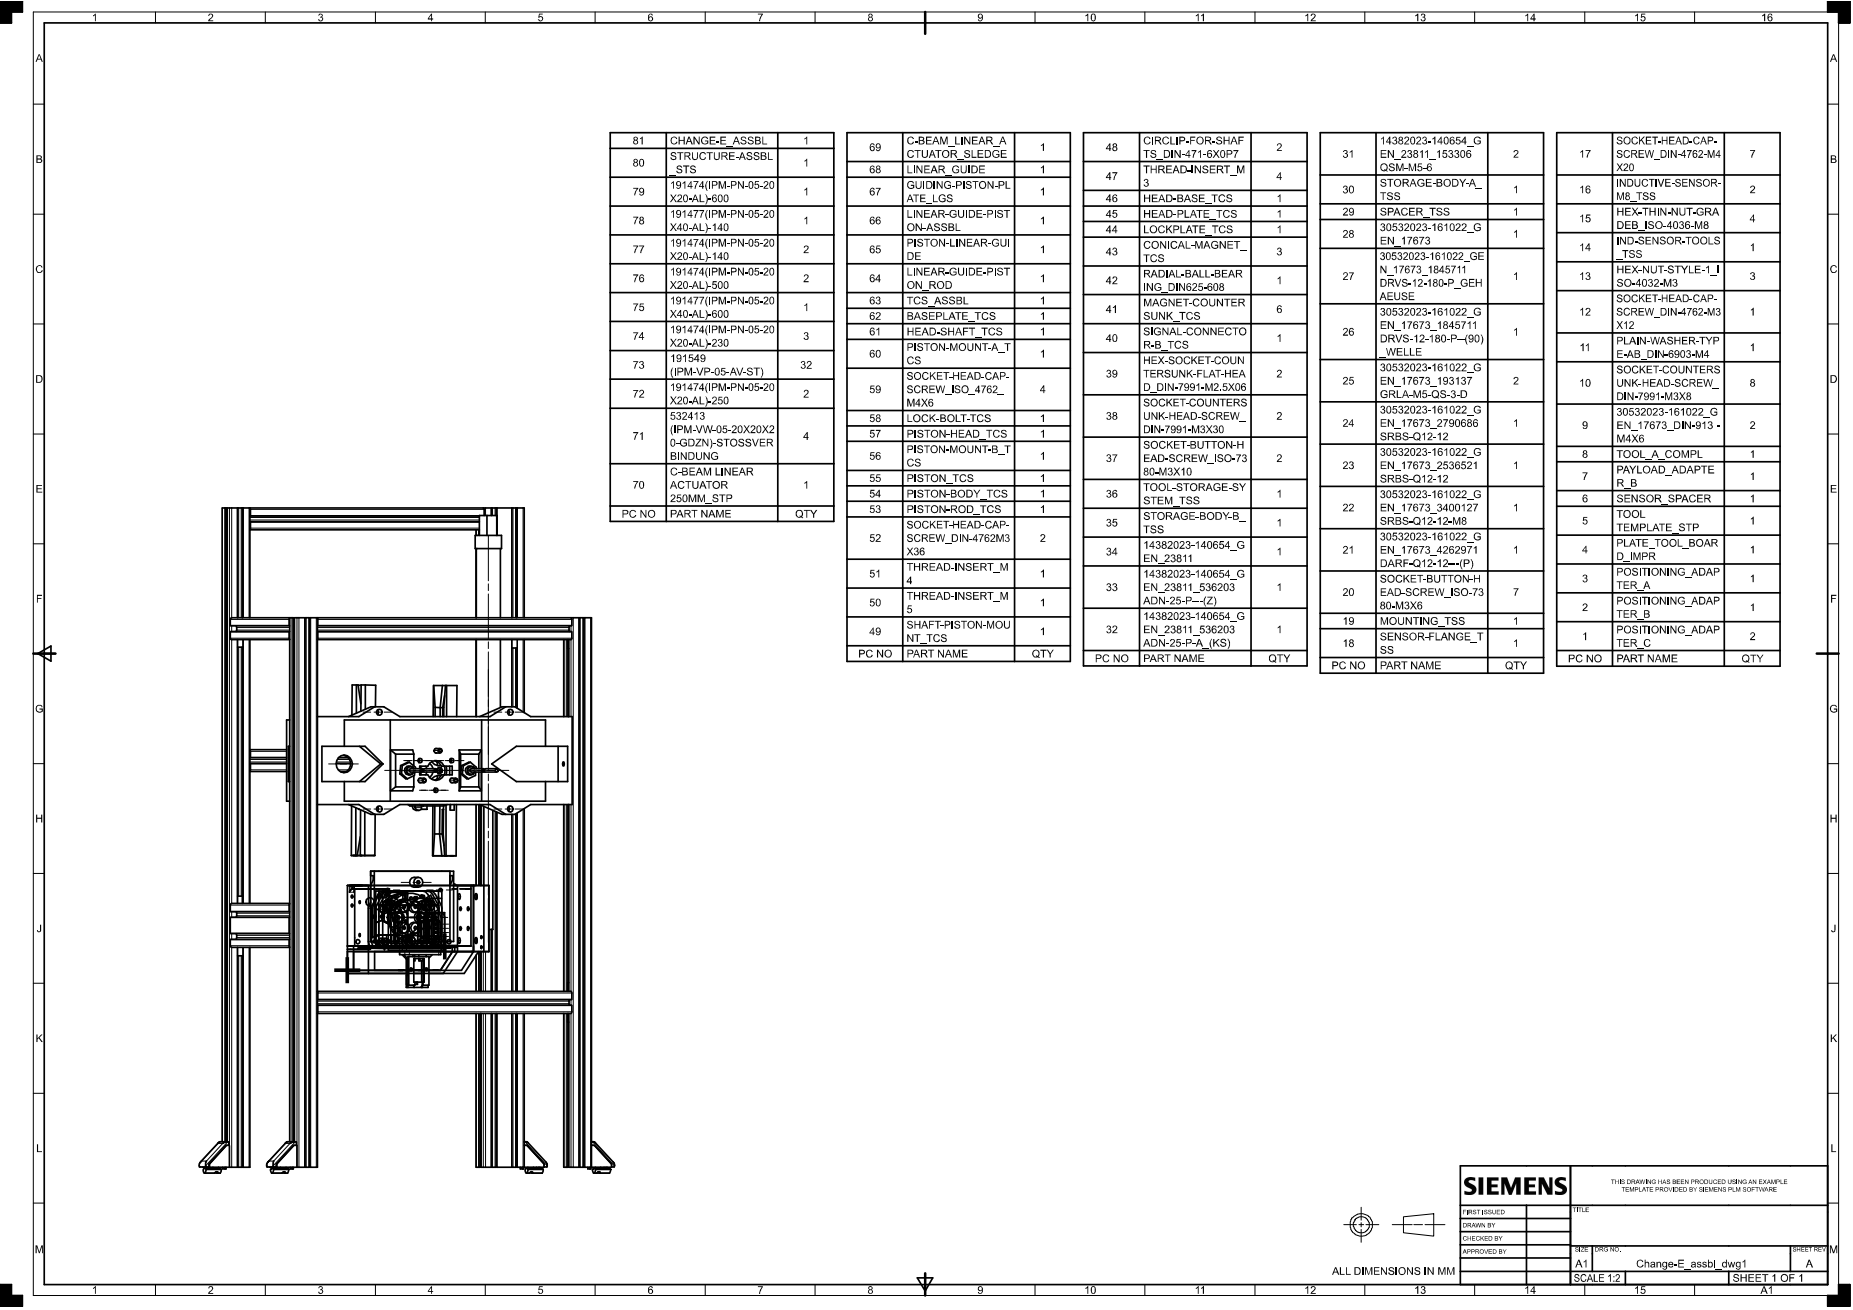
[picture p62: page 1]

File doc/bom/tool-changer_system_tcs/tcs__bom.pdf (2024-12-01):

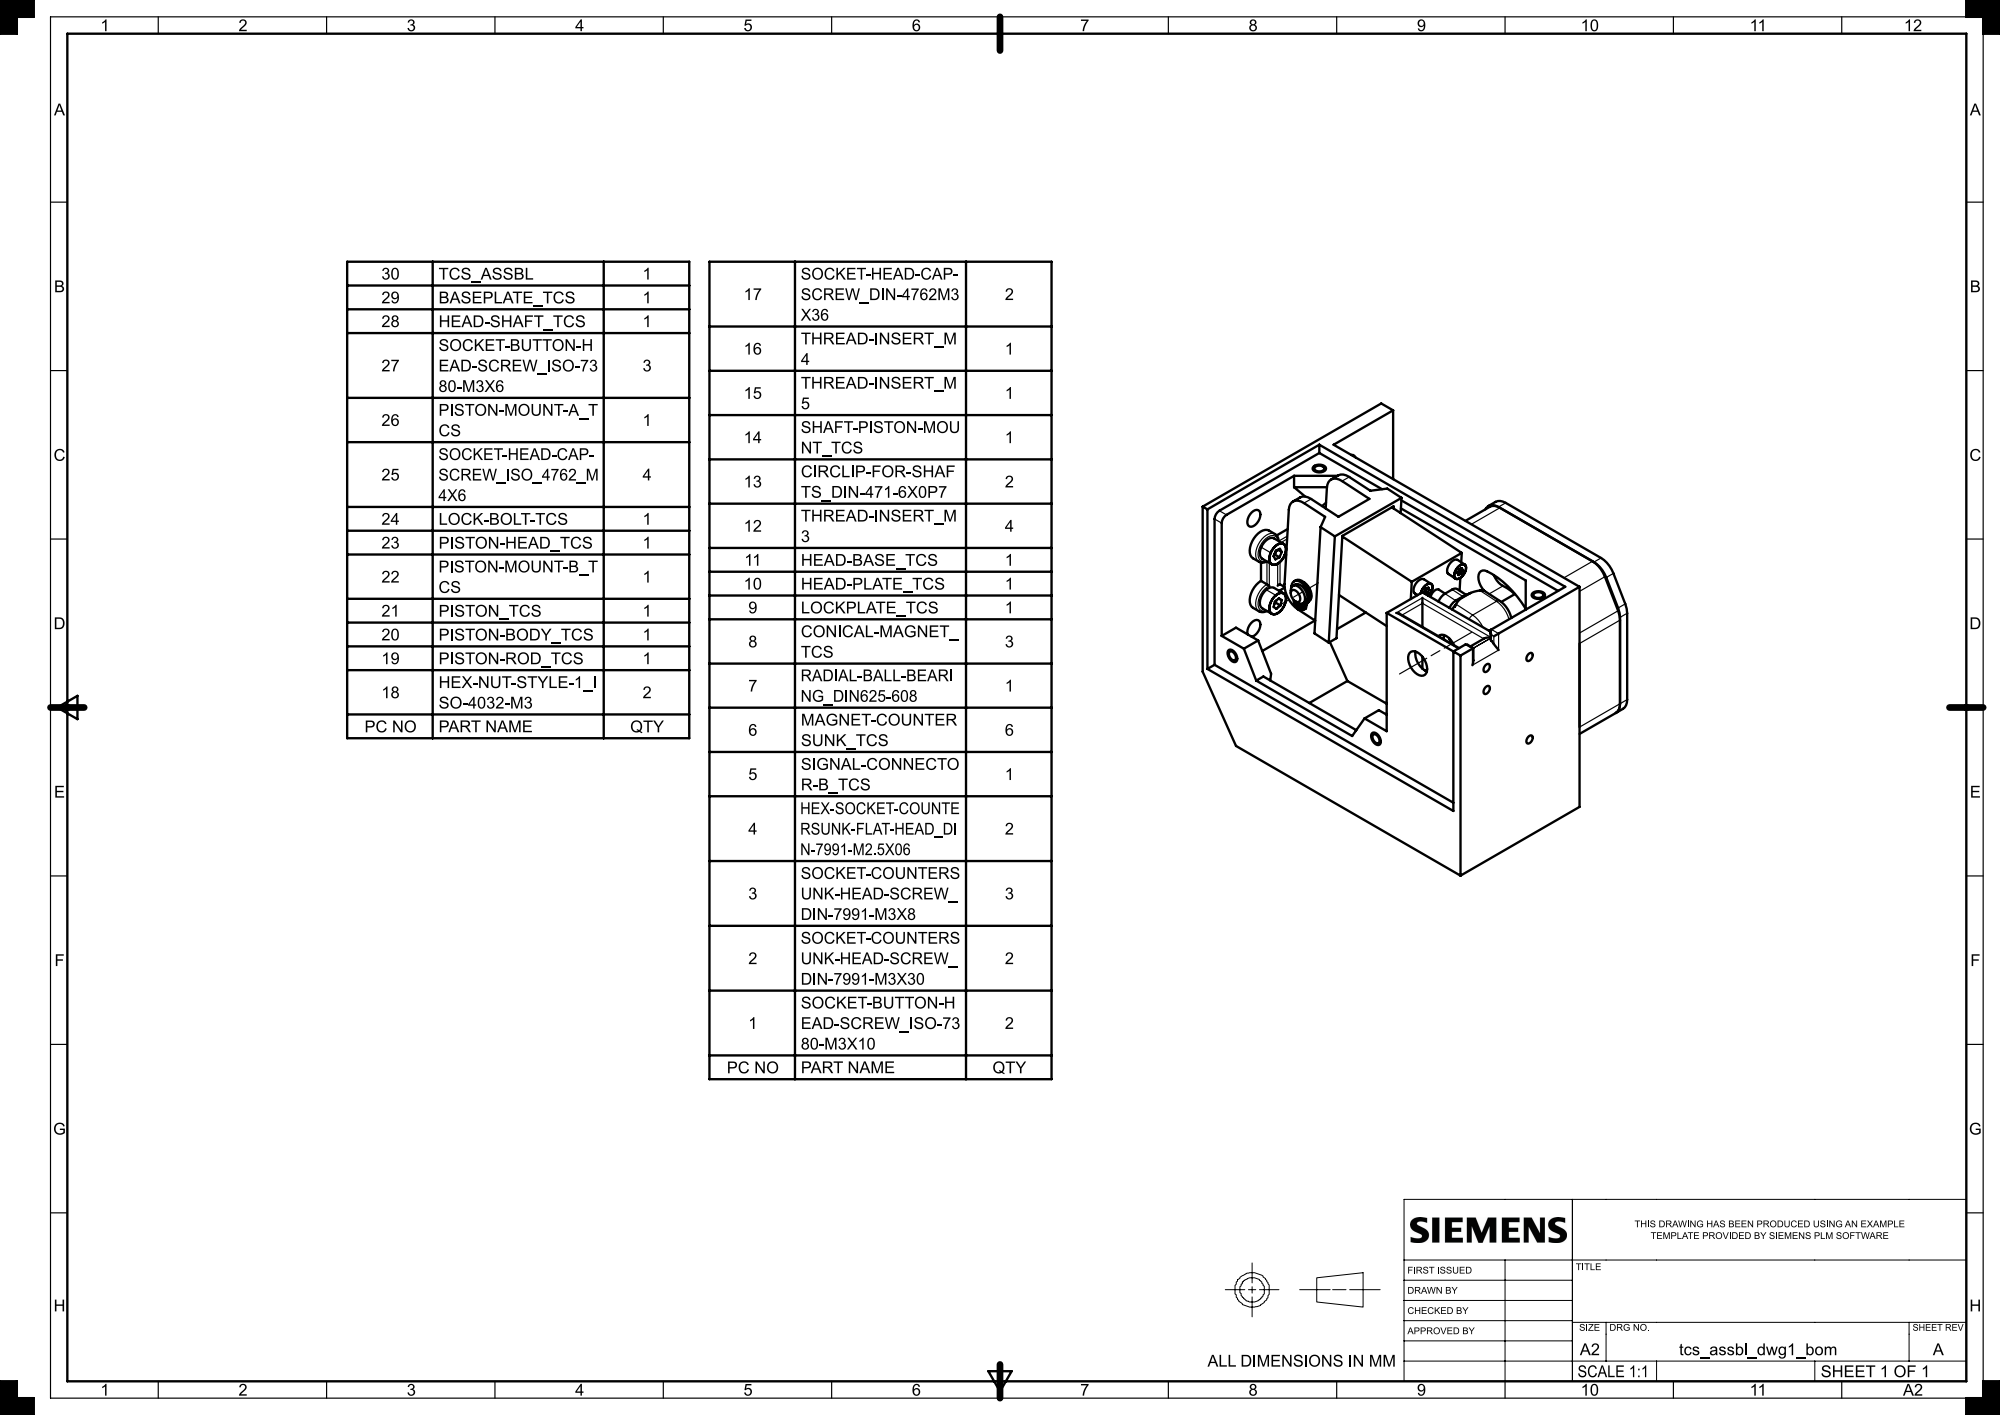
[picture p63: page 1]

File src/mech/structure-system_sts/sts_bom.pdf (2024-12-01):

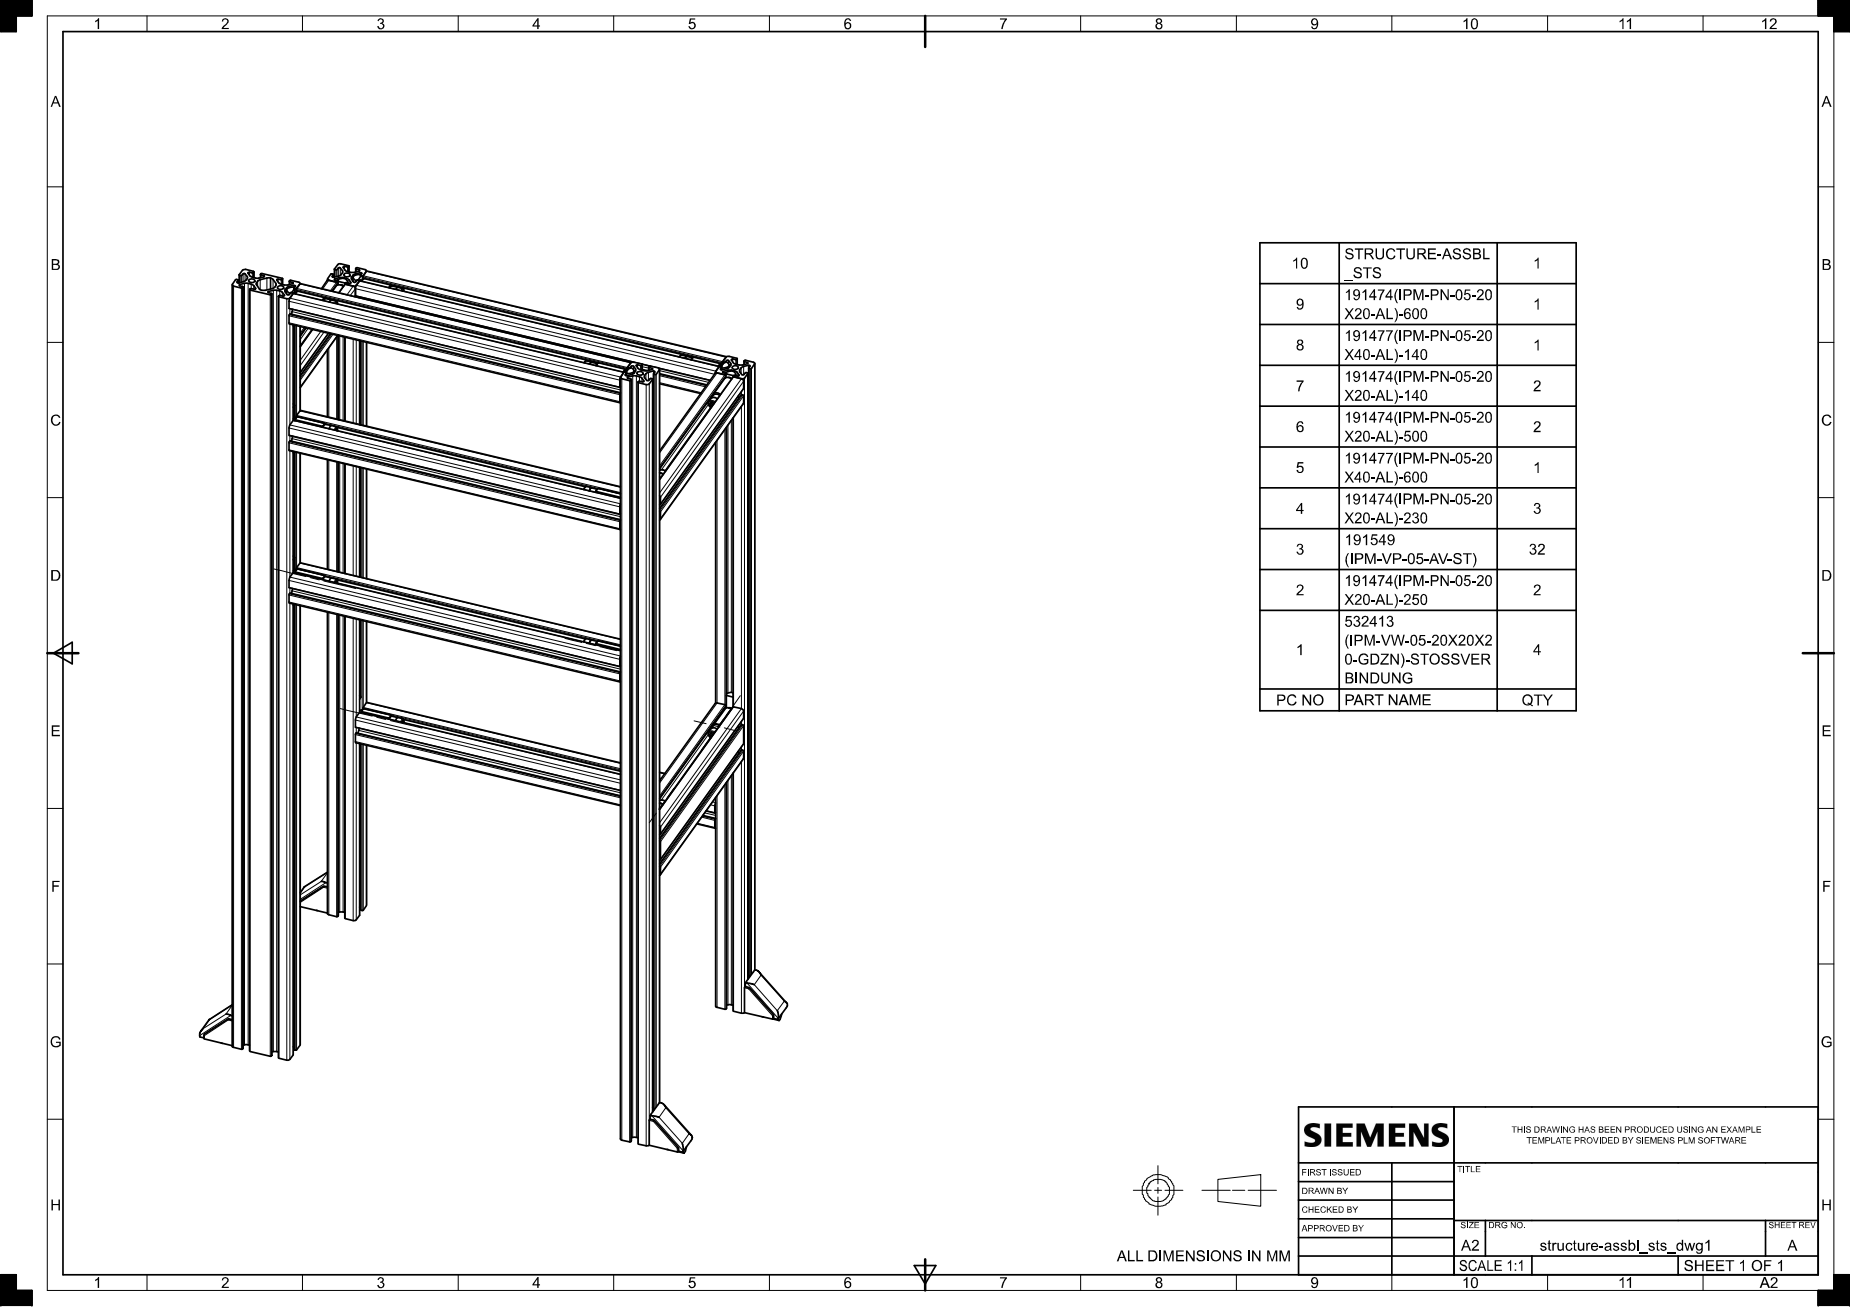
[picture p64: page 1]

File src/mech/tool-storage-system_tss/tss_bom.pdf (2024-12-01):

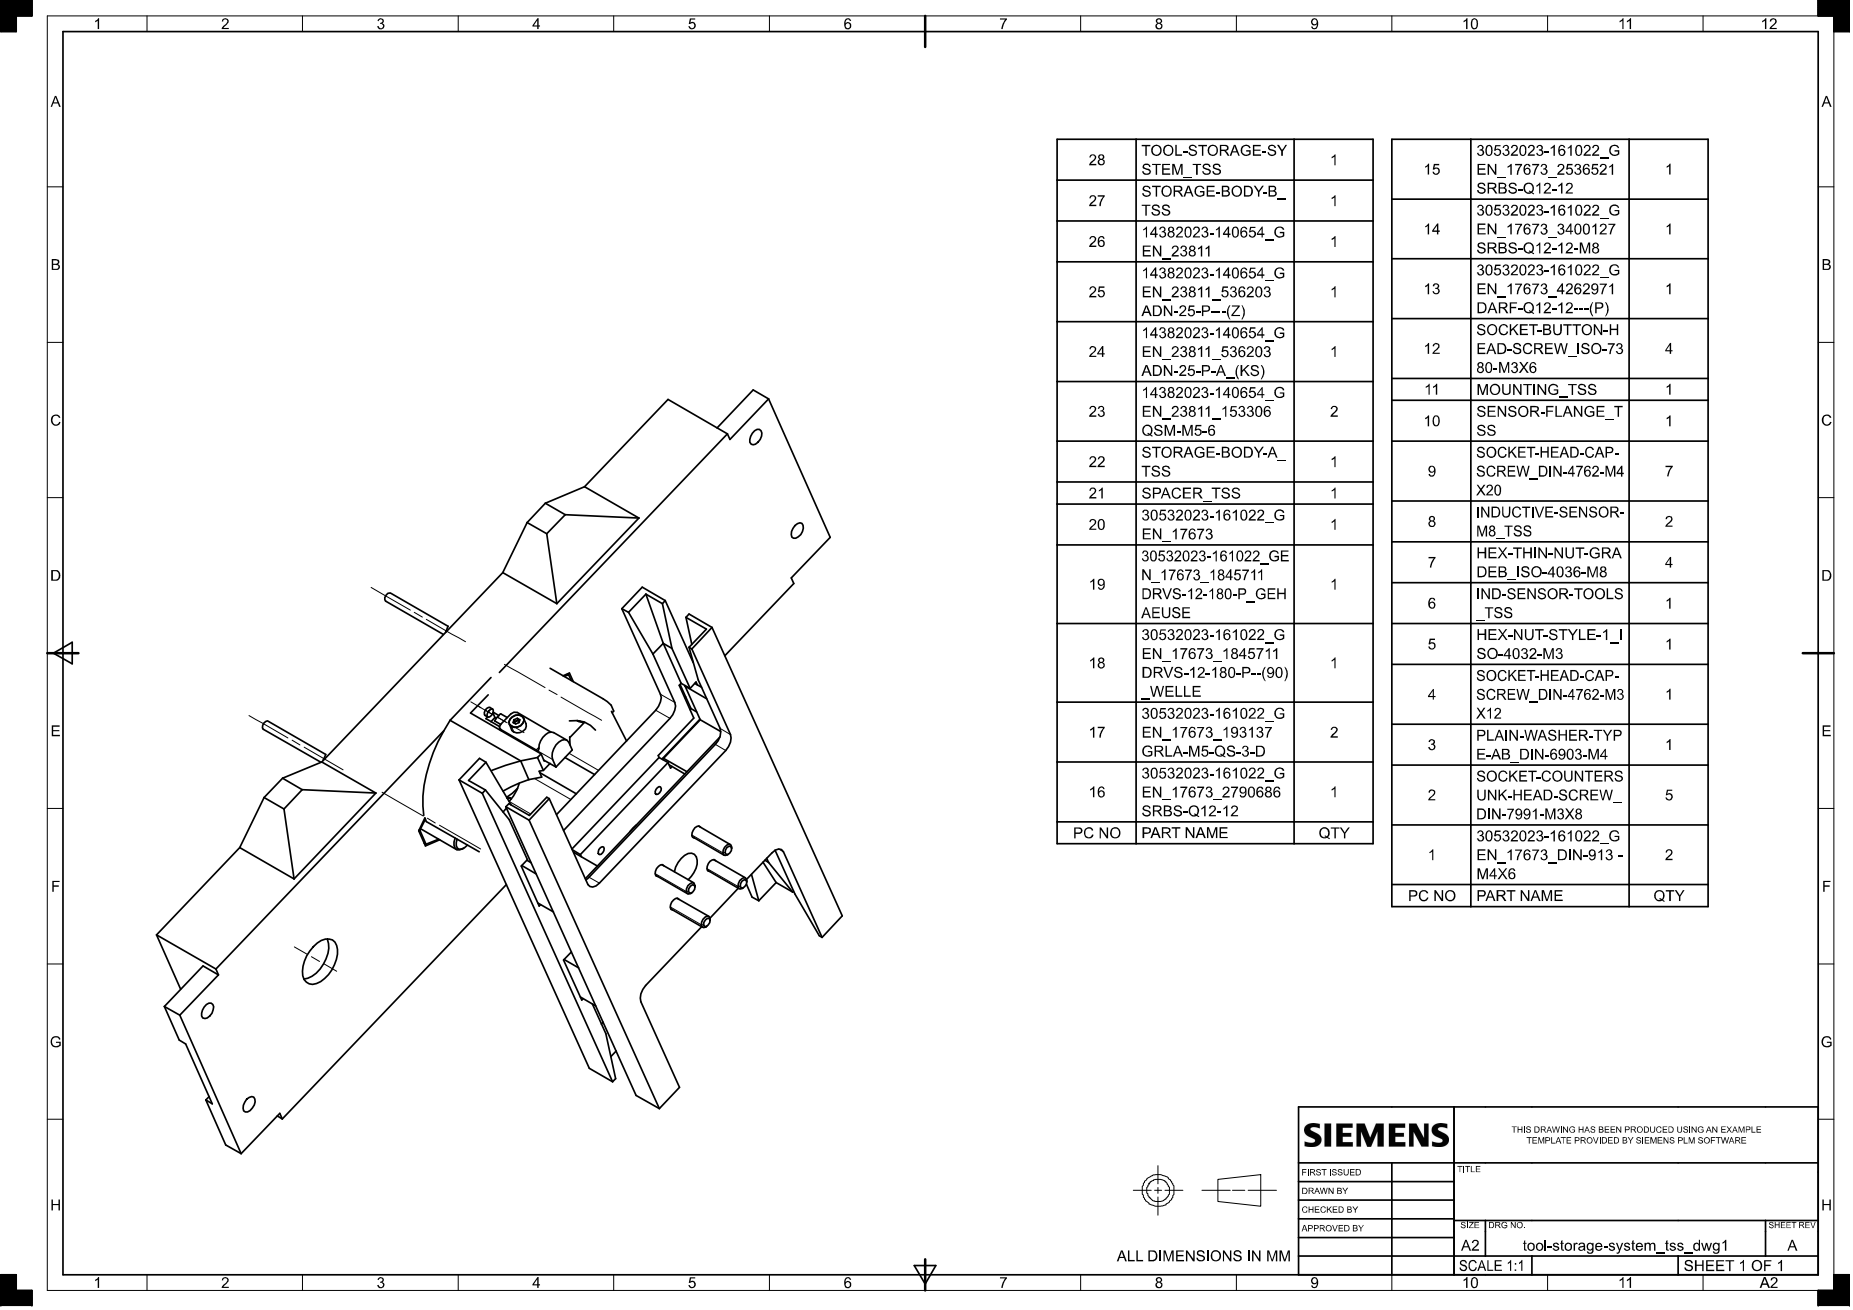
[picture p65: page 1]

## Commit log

2024-12-01 - Update README.md - TOC removed for GitHub - proprietary models dropped
    [191474(IPM-PN-05-20x20-AL)-140.prt, 191474(IPM-PN-05-20x20-AL)-140_new.prt, 191474(IPM-PN-05-20x20-AL)-160.prt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]
2024-12-01 - new version - linear drive changed to pneumatic piston - tools added
    [191474(IPM-PN-05-20x20-AL)-140.prt, 191474(IPM-PN-05-20x20-AL)-140_new.prt, 191474(IPM-PN-05-20x20-AL)-160.prt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]
